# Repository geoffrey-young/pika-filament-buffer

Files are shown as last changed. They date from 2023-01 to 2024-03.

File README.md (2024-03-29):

# piKa - a multimaterial filament buffer solution

---

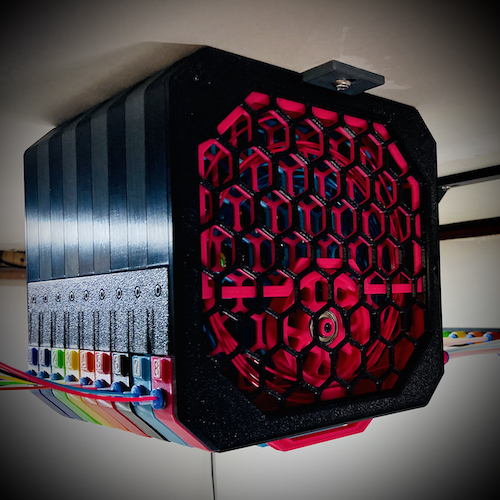
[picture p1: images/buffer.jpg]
buffer
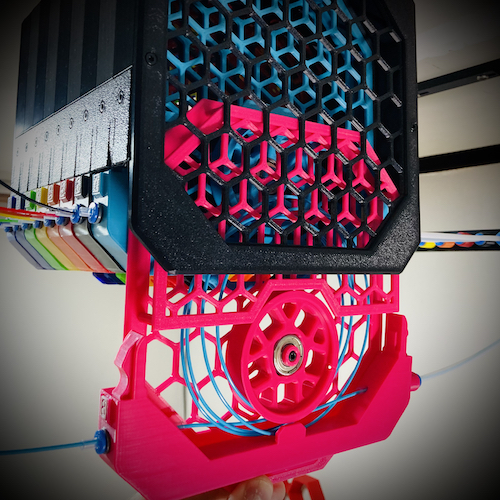
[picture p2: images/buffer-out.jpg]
buffer out
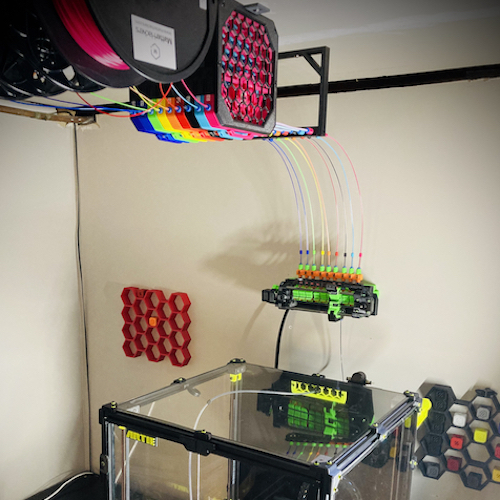
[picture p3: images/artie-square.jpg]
artie
|  |  |  |
| :---: | :---: | :---: |
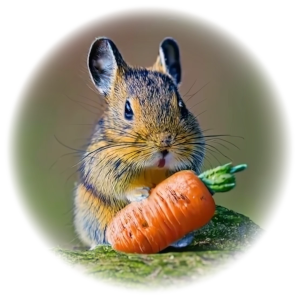
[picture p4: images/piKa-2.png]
piKa
| |  | |

---

## welcome

thanks for checking out [piKa](#pika), the friendly [ercf](https://github.com/EtteGit/EnragedRabbitProject) filament buffer.

now let's get to it...

* [operation](#operation)
* [how much can I buffer?](#how-much-can-i-buffer)
  + [testing](#testing)
  + [limitations](#limitations)
* [BOM](#bom)
  + [a note on magnets...](#a-note-on-magnets)
  + [m2x8 hex cap self threading screws](#m2x8-hex-cap-self-threading-screws)
* [printing](#printing)
* [assembly](#assembly)
  + [manual](#manual)
  + [video](#video)
  + [array](#array)
  + [buffer segments](#buffer-segments)
  + [tag plates](#tag-plates)
* [mounting](#mounting)
* [pictures](#pictures)
* [why?](#why)
* [piKa?](#pika)
* [credits](#credits)
* [contributing](#contributing)
* [other buffer options](#other-buffer-options)

---

## operation

buffer operation made simple...

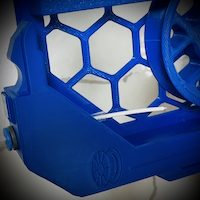
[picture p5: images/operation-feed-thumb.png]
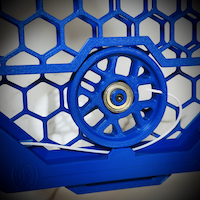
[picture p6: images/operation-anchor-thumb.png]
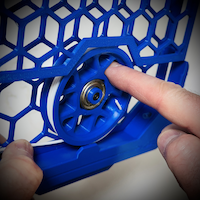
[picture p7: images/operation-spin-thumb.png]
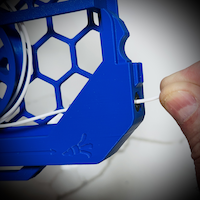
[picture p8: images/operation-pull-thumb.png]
      

there's also a video of the buffer in action I posted on discord that's worth a look:

- https://discord.com/channels/460117602945990666/708772910956937336/1038298353324273754

the number of people who haven't figured out the spin-the-wheel-with-your-finger method is significantly higher than I would have imagined.

"but how fast and easy is it to load... really?" I hear you cry.  allow satisfied discord user `@ningj V2.2726` to show you:

- https://discord.com/channels/460117602945990666/909743915475816458/1089361904650162266

## how much can I buffer?

my `ercf_calib_ref` is currently `1146.4` and I use 5 loops.

beyond that, my tests indicate the [standard wheel](stl/[a]_buffer-wheel_xN.stl) can successfully buffer ~300mm per loop up to 6 loops:

| loops | buffer capacity |
| :---  | :--- |
| 1 | 300mm | 
| 2 | 600mm | 
| 3 | 900mm | 
| 4 | 1200mm | 
| 5 | 1500mm | 
| 6 | 1800mm | 
| 7+ | not recommended | 

### testing

I've added the [klipper macro](./klipper/pika.cfg) I use to test repeated buffer load/unload cycles, which is a great way to exercise your setup without printing.

***!!! you must remove the bowden from the toolhead before running this macro.  you've been warned !!!***

### limitations

pika performance is steady and reliable up to 6 loops, which should provide more than enough for the vast majority of setups.

at 7+ loops two gremlins start to reveal themselves...

the first gremlin is that the filament begins to be more prone to tangling during or after the load sequence.  experimentation has led me to believe this is mostly due to limitations of the [standard wheel](stl/[a]_buffer-wheel_xN.stl) design.

the second gremlin is more insidious in that the weight of the buffered filament begins to compound - once you load 300mm it takes more push to slosh the next 300mm of filament back and coil it up in the cage.  after around 2000mm or so of filament the ercf gear isn't as successful in pushing all the filament along and the consistency of the buffer process begins to degrade.  

the former problem I'm beginning to solve with a [new wheel concept](https://github.com/geoffrey-young/pika-filament-buffer/tree/v2-wheel-beta/v2-wheel-beta), while no wheel design can counteract the laws of physics governing the latter.  I'm still giving this latter gremlin some thought...

## BOM

here is the hardware you'll need.  hopefully this is a full, accurate list...

| item | 3 cart total | 6 cart total | 8 cart total | 9 cart total | 12 cart total |
| :--- | :--- | :--- | :--- | :--- | :--- |
| m3x8 (or m3x10) | 23 | 38 | 48 | 53 | 68 |
| m3x8 (or m3x10) flat head | 6 | 12 | 16 | 18 | 24 |
| m3x12 | 3 | 6 | 8 | 9 | 12 |
| m3 heatset (standard voron m3 x 5mm x 4mm) | 12 | 24 | 32 | 36 | 48 |
| [m2x8 self tapping](#m2x8-hex-cap-self-threading-screws) | 21 | 42 | 56 | 63 | 84 |
| 608 bearing | 3 | 6 | 8 | 9 | 12 |
| ecas connector | 6 | 12 | 16 | 18 | 24 |
| [10x3 disc magnet with 3mm hole](#a-note-on-magnets) (optional) | 6-12 | 12-24 | 16-32 | 18-36 | 24-48 |
| PTFE/FEP 4mm OD x (2.5mm or 3.0mm ID) tubing | variable | variable | variable | variable | variable |

note that all of the m3x8 screw holes are long enough to accept m3x10

plus mounting hardware if you want to use the bottom bracket to mount the array on something.

the majority of the hardware was selected due to it being common across voron builds, so folks will likely have it just sitting around.  the big exception being the hole magnets...

### a note on magnets...

I used 10x3 disc magnets ~~[from amazon]()~~, which seem to be a moving target. basically, you're looking for 10x3 disc magnets with a 3mm hole in the middle, like these:

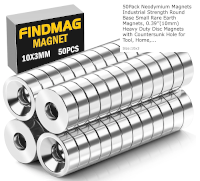
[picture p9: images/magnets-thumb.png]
magnets


magnets with 4mm holes are a little better, but outside of the very first set I ordered I haven't been able to find any.

**just a small wrinkle...** as with the "6x3mm" magnets for the ercf and other voron projects, parts are designed against sizes most commonly provided by suppliers.  in our case, the majority of "10x3mm" hole magnets in the wild are really around 9.5mm in diameter.  as such, piKa parts are designed against this width.

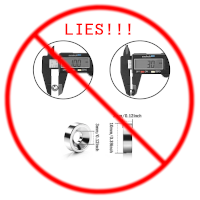
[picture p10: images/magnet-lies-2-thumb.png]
magnet-lies-2
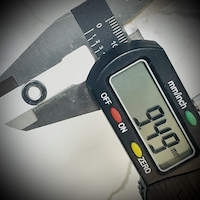
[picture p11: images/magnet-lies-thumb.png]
magnet-lies
 

if you have true 10x3mm magnets they'll be too large for the standard magnet tops and connectors.  the good news is that you now have options.

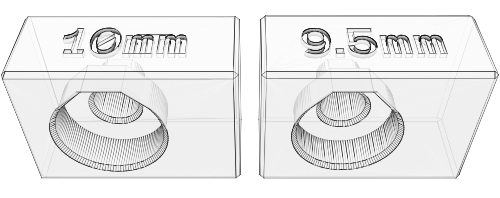
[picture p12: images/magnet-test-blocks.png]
magnet test blocks


after printing the [magnet test blocks](./stl/10mm-magnets/magnet-test-blocks.stl) to verify your fit, the [10mm](./stl/10mm-magnets/) directory has the files you'll need.

### m2x8 hex cap self threading screws

these m2x8 hex cap self threading screws [from amazon](https://www.amazon.com/gp/product/B00YBMRAH4) are really handy, both for this and other voron projects, like klicky.  m2x10 will also work if those are easier to find.  

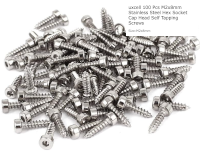
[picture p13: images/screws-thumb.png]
screws


## printing

a few things to note when printing...

- **the models already oriented for optimal printing**.  no parts have included supports to remove, nor are supports necessary for any part.  if there are overhangs that need support the part is oriented incorrectly.
- due to bending of large parts, you want to **print the bottoms flat so that the latch fit is tight** - you'll only be able to print 1 or two of these at a time.
- conversely, **the tops are designed to be printed upright**, so go ahead and fill your plate.  if you care about a good looking bottom overhang, keep your exterior perimeter fans at 100% and engage them starting on layer 2.
- I used 20% infill on the tops and bottoms in order to keep parts light and plastic use down.  **ymmv**.
- I would suggest printing the latches and bracket using standard voron parameters (40% infill, .2mm layers, 4 perimeters) for added strength.
- the screen with the posts works best with higher temps and lower fan to keep the layers as strong as possible.  early versions had thinner posts, but the current version is a bit more rigid and should be less problematic.
- consider using setting `only_one_perimeter_first_layer` to `true` for the screens, which helps the first layer be a little more sane.  well, in superslicer, anyway.

I printed mine in ABS, and most people do the same.  PLA should be fine, but ymmv...

## assembly

hopefully, y'all find this self explanatory, and can figure it out from the pictures.  basically, we have:

- a series of buffer slot slider thingies
- held together by a frame

that's about it.

the good news is that there's only one way the parts can really go together, and everyone so far has found it relatively straightforward.

and in late breaking news, there's even [a manual](./assembly-manual.pdf) and a [video][#video]!

feel free to ping me on the [voron discord](https://discord.com/channels/460117602945990666/869236671554682990) in [`#ercf_questions`](https://discord.com/channels/460117602945990666/909743915475816458) if you have issues.  

### manual

and now... [a manual](./assembly-manual.pdf)

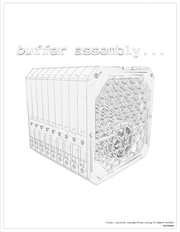
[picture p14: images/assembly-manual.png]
manual


### video

recently, @MakerMylo created a [video](https://youtu.be/PdVolU5ywEg) of an [8 cart pika build](https://www.printables.com/model/776988-8-lane-pika-filament-buffer-ercf-v2) which you may find helpful as well.

### array

currently, there are 6, 9, and 12 slot versions for [ERCF classic](https://github.com/EtteGit/EnragedRabbitProject), plus an 8 cart version for [ERCF v2](https://github.com/Enraged-Rabbit-Community/ERCF_v2).

the only parts that differ depending on the number of slots are the side latches and bottom bracket.

the 9 cart is the most popular, and what I currently run. both the 6 and 12 cart versions have at least one user I've worked through the design with, so I'm confident in the dimensional accuracy. however, if you discover an issue with the sizing just let me know.

| part | description | required hardware | 
| :--- | :--- | :--- |
| [`array-front.stl`](stl/array-front.stl) | front of array | m3x8 (or m3x10) | 
| [`array-front-screen.stl`](stl/array-front-screen.stl) | screen for front of array | none | 
| [`array-back.stl`](stl/array-back.stl) | back of the array | m3x8 (or m3x10) |
| [`array-latch-9a.stl`](stl/array-latch-9a.stl) | side latch (stls for 3, 6, 8, and 12 cart versions also provided) | m3x8 (or m3x10) |
| [`array-latch-9b.stl`](stl/array-latch-9b.stl) | side latch (stls for 3, 6, 8, and 12 cart versions also provided) | m3x8 (or m3x10) |
| [`array-bottom-bracket-9.stl`](stl/array-bottom-bracket-9.stl) | bottom bracket (stls for 3, 6, 8, and 12 cart versions also provided) | m3x8 (or m3x10) |

### buffer segments

one complete buffer is required per cart, so for a nine cart system `_xN` turns in to `_x9` and you print 9 of that piece.

two buffer top configurations are provided:

* [one ecas end and one disc magnet end](stl/[a]_buffer-top-ecas+magnet_xN.stl)
* [two disc magnet ends](stl/[a]_buffer-top-magnet+magnet_xN.stl)

which configuration you choose depends on the needs of your setup.  

please see [the note on magnets](#a-note-on-magnets), and check out the [10mm magnet options](./stl/10mm-magnets/) as required. 

| part | description | required hardware |
| :--- | :--- | :--- |
| [`buffer-bottom_xN.stl`](stl/buffer-bottom_xN.stl) | segment bottom | m3 heatset |
| [`[a]_buffer-top-ecas+magnet_xN.stl`](stl/[a]_buffer-top-ecas+magnet_xN.stl) | segment top, one side ecas and one side disc magnet connector | ecas, [9.5mm disc magnet](#a-note-on-magnets) |
| [`[a]_buffer-top-magnet+magnet_xN.stl`](stl/[a]_buffer-top-magnet+magnet_xN.stl) | segment top, both sides disc magnet connector | ecas, [9.5mm disc magnet](#a-note-on-magnets) |
| [`[a]_ecas-to-magnet-end_xN.stl`](stl/[a]_ecas-to-magnet-end_xN.stl) | if you use either of the magnet tops | ecas, [9.5mm disc magnet](#a-note-on-magnets) |
| [`[a]_buffer-screen-a_xN.stl`](stl/[a]_buffer-screen-a_xN.stl) | segment screen for wheel | m3x8 (or m3x10) flat head, m3 heatset |
| [`[a]_buffer-screen-b_xN.stl`](stl/[a]_buffer-screen-b_xN.stl) | segment top screen | [m2x8 self tapping](#m2x8-hex-cap-self-threading-screws) |
| [`[a]_buffer-bearing-insert_xN.stl`](stl/[a]_buffer-bearing-insert_xN.stl) | holds the wheel in place | m3x12 |
| [`[a]_buffer-handle_xN.stl`](stl/[a]_buffer-handle_xN.stl) | segment handle | m3x8 (or m3x10) |
| [`[a]_buffer-wheel_xN.stl`](stl/[a]_buffer-wheel_xN.stl) | wheel | 608 bearing |

the wheel is (currently) almost exactly the same as the ercp wheel...  however, I strongly suggest *not* using the stock ercf wheel - the pika wheel has a slightly different bearing offset so that it sits next to the screen properly, as well as a hole for loading so you are less likely to cross filament on the wheel.

### tag plates

if you mount your buffer overhead your numbers will be upside down.  you can find upside down tag plates [here](https://github.com/geoffrey-young/3D-Printing/tree/main/models/voron/ercf/upside-down-numbers).

## mounting

in general I'm not a fan of sticking the ercf on my printer - something just makes me think all that extra weight and loose pieces rattling around can't be good for my resonance compensation efforts.

with that in mind, I mount my ercf on the wall at 90 degrees using a french cleat system, which you can find [here](https://github.com/geoffrey-young/3D-Printing/tree/main/models/voron/ercf/mounts/ercf-french-cleat).

the 90 degree mounting created some challenges accessing the filament block ecas connectors, so I made [an extension](https://github.com/geoffrey-young/3D-Printing/tree/main/models/voron/ercf/extender) to help.

a magnetic bowden "bridge" (plus some springs) keeps my bowden tubes straight, clear, and managed.  available [here](https://github.com/geoffrey-young/3D-Printing/tree/main/models/voron/ercf/mounts/bridge).

## pictures

some reference photos, videos, etc

| artie `v2.1650` | | |
| :--- | :--- | :--- |
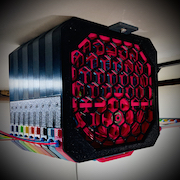
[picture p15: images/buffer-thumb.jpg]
buffer
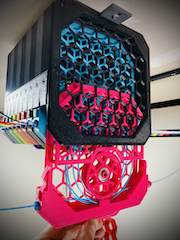
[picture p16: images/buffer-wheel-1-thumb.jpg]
buffer wheel
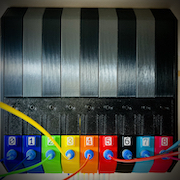
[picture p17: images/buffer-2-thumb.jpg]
buffer 2
|  |  |  |
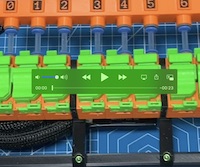
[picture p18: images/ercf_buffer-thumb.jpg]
movie (https://discord.com/channels/460117602945990666/708772910956937336/1038298353324273754)
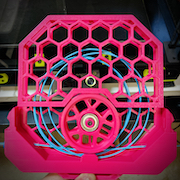
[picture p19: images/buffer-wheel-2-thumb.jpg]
buffer wheel 2
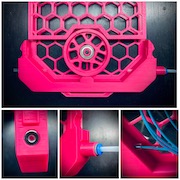
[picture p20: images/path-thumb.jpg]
path
|  |  |  |
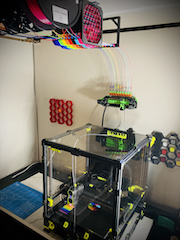
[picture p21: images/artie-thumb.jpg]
artie
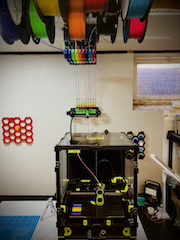
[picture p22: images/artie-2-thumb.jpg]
artie 2
|  |  | assembly manual |

| other users on discord | | |
| :--- | :--- | :--- |
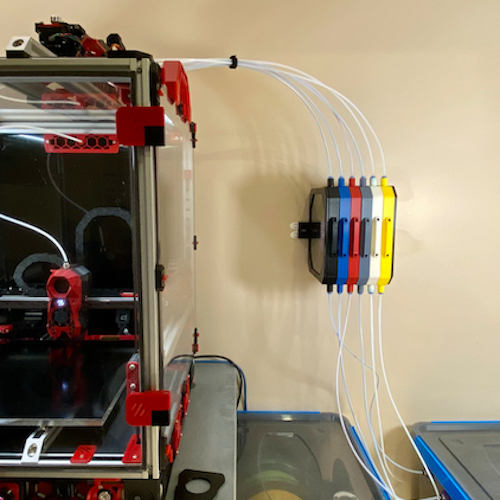
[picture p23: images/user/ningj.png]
ningj-1
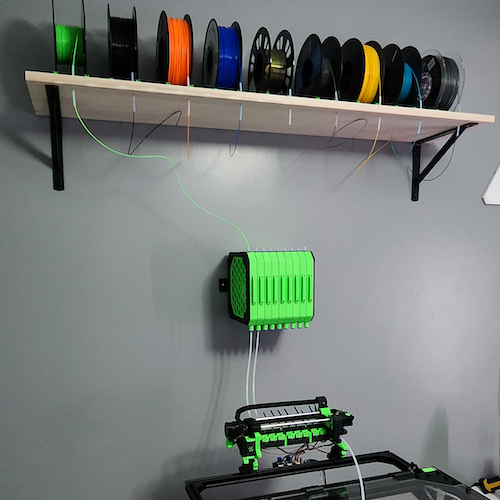
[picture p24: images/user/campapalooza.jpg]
campapalooza-1
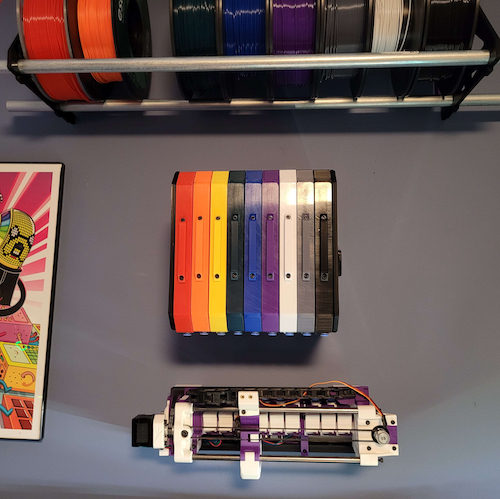
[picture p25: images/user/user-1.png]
user-1
|  |  |  |
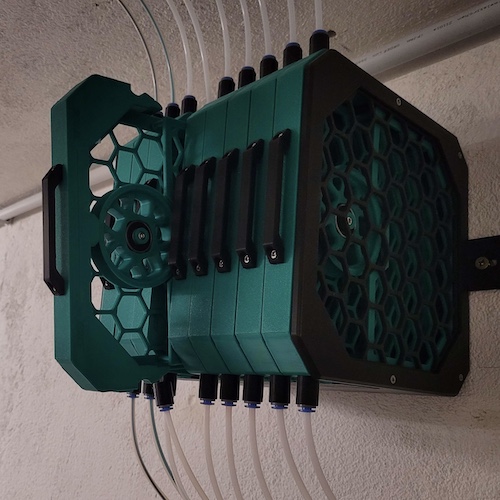
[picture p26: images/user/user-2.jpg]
user-2
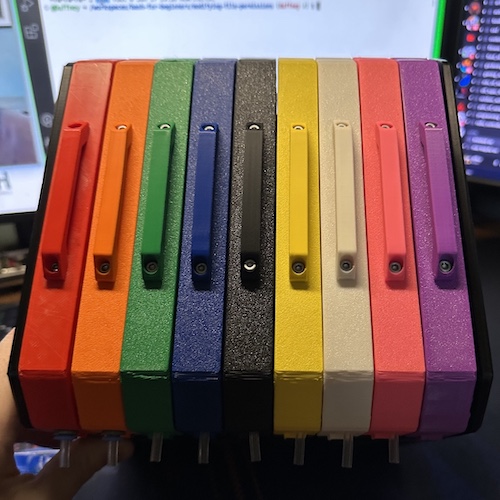
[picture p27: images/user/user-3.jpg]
user-3
|  |  | |

pull requests against the [current development branch](#contributing) with your (single 500x500px) picture added to `images/user/` most welcome.

## why?

filament buffers are hard™

I didn't realize how hard until I ventured down this path.

I started like most do, and loyally printed some [ercf carrot patch](https://github.com/EtteGit/EnragedRabbitProject/tree/main/Carrot_Patch) units.  space limitations required me to mount them overhead, which is where things started to go sideways - every time I needed to put in new filament I had to find a chair and fsck around with the confined carrot patch space, sharp edges, filament whiplash, and whatnot - all overhead - until my shoulders hurt, cursing the entire time.  I figured there had to be a better way...  

it turns out, there really wasn't...  at least not at the time.  since then, the community has been kind enough to generate a few [different buffer options](#other-buffer-options), each with its unique set of benefits and drawbacks depending on your needs, setup, and tolerance.  all of them are better than the original ercp, imho, which is good for everyone.  however, I'm of the opinion that they all still have drawbacks, leaving us still chasing the platonic ideal filament buffer solution...

still, way back then all I wanted was a lightning-fast, super-simple, overhead-mounted, expletive-free, wheel-based, wicked-dependable filament buffer solution.  how hard could it be?

this thing here is where I ended up.

honestly, I'm surprised it actually worked... but it really does, and my experience has been frustration free ever since.  others on discord seem to have similarly joyful experiences with it as well, so I guess I'm on to something.

## piKa?

### ***in chemistry...***

a [buffer](https://en.wikipedia.org/wiki/Buffer_solution) is a solution specifically designed to be resistant to changes in pH, allowing a reaction to continue in balance even when ideal conditions are threatened.  the most effective buffers  - those with the greatest capacity to absorb change - are created using an acid whose **p**___Ka___ (acid dissociation constant) is equal to the desired pH.  choosing an acid with the wrong **p**___Ka___ can mean disaster.

**p**___Ka___ is crucial to buffer efficacy

### ***in taxonomy...***

three members make up the order [Lagomorpha](https://en.wikipedia.org/wiki/Lagomorpha): rabbits, hares… and pikas

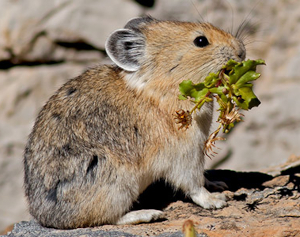
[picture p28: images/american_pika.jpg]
american pika (https://www.nwf.org/Educational-Resources/Wildlife-Guide/Mammals/American-Pika)

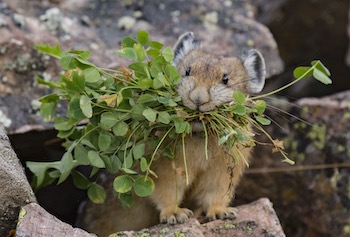
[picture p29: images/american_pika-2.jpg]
american pika (https://www.biographic.com/dine-and-dash/)


pretty cool little creatures, worth getting to know.

### ***in multimaterial 3d printing...***

we have a [rabbit](https://github.com/EtteGit/EnragedRabbitProject), and a [hare](https://github.com/moggieuk/Happy-Hare), and now... a pika

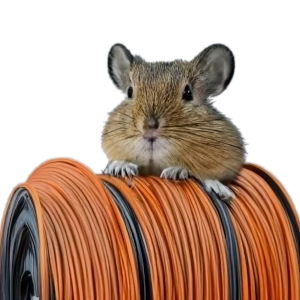
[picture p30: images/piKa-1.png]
piKa


buffers, solutions, p*Ka*... the name just seemed to come together for a recovering chemist.

## credits

- the entire concept here started after seeing [this mmu buffer on printables.com](https://www.printables.com/model/30811-mmu-slot-buffer).  while my work isn't really a mod of that (I modeled everything myself from scratch), I did copy the latch concept nearly... verbatim?  I'm sure there's a word for it.  anyway, the latch works really well, and needless to say I couldn't have figured a mechanism like that on my own.  this project owes sincere credit and gratitude to all the work and effort over there.  many thanks!

- all the fittings and cutouts - ecas and m3 holes, bridging, etc - were taken directly from either the [ercf project](https://github.com/EtteGit/EnragedRabbitProject) or the [voron 2.4 project](https://github.com/VoronDesign/Voron-2/).  since I use blender and don't cad, I really appreciate all the community work that has gone into getting those measurements and fit tricks just right.  kudos to team voron, be they enraged or not.

- the buffer wheel is taken right from [ercf project](https://github.com/EtteGit/EnragedRabbitProject).  no need to reinvent the wheel...

- [deepfriedhero](https://dfh.fm), [west3d](https://west3d.com), and [fabreeko](https://www.fabreeko.com) for consistently fantastic parts and service

- I'm super grateful for some early beta testers, who provided really valuable feedback:
  - `@TheTechRunner V2.1453 V0.1556`
  - `@ningj V2.2726`
  - `@ZChem V2.5299`
  - `@SilentMuse V2.3841`
  - `@Imburr VT.959`
  - `@xF4m3 V2.3687`

- probably others - if you feel left out let me know :)

## contributing

pull requests against [the `dev` branch](https://github.com/geoffrey-young/pika-filament-buffer/tree/v2-wheel-beta/) more than welcome.  feel free to dm me over in discord to discuss something first.

be sure to read the [LICENSE](./LICENSE) and mentally agree with it.  please don't make me add license acknowledgement and sign-off overhead to the project - we're all just after a kinder buffer experience so we can get on with printing, so let's just focus on that, ok?

## other buffer options

some other community buffers that may suit your needs:

- [carrot quiver](https://github.com/SkiBikePrint/ERCF_Mods/tree/main/Carrot_Quiver_Buffer)
- [stern wheeler](https://www.printables.com/model/472316-stern-wheeler)
- [cotton tail](https://github.com/Enraged-Rabbit-Community/ERCF_v2/blob/master/Recommended_Options/ERCT_Buffer)

I suggest asking on discord about these other buffers and their strengths and weaknesses and decide what buffer is best for your situation.

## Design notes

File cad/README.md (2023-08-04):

# where's the CAD?

I do all my modeling with [blender](https://www.blender.org), so there are unfortunately no CAD files for sharing.

someday I may learn CAD... but probably not

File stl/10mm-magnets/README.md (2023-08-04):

# 10x3mm magnet support

as discussed in [a note on magnets...](../../README.md#a-note-on-magnets) in the [README](../../README.md), true 10x3mm disc magnets are a rare find in the wild.  however, if you happen to get some below are the files you'll need.

please print the [disc magnet test blocks](./magnet-test-blocks.stl) and test fit your magnets before printing actual parts.

magnet test blocks

---

| part | description |
| :--- | :--- |
| [`[a]_10mm-buffer-top-ecas+magnet_xN.stl`](stl/10mm-magnets/[a]_10mm-buffer-top-ecas+magnet_xN.stl) | segment top, one side ecas and one side 10x3mm disc magnet connector |
| [`[a]_10mm-buffer-top-magnet+magnet_xN.stl`](stl/10mm-magnets/[a]_10mm-buffer-top-magnet+magnet_xN.stl) | segment top, both sides 10x3mm disc magnet connector |
| [`[a]_10mm-ecas-to-magnet-end_xN.stl`](stl/10mm-magnets/[a]_10mm-ecas-to-magnet-end_xN.stl) | if you use either of the magnet tops |

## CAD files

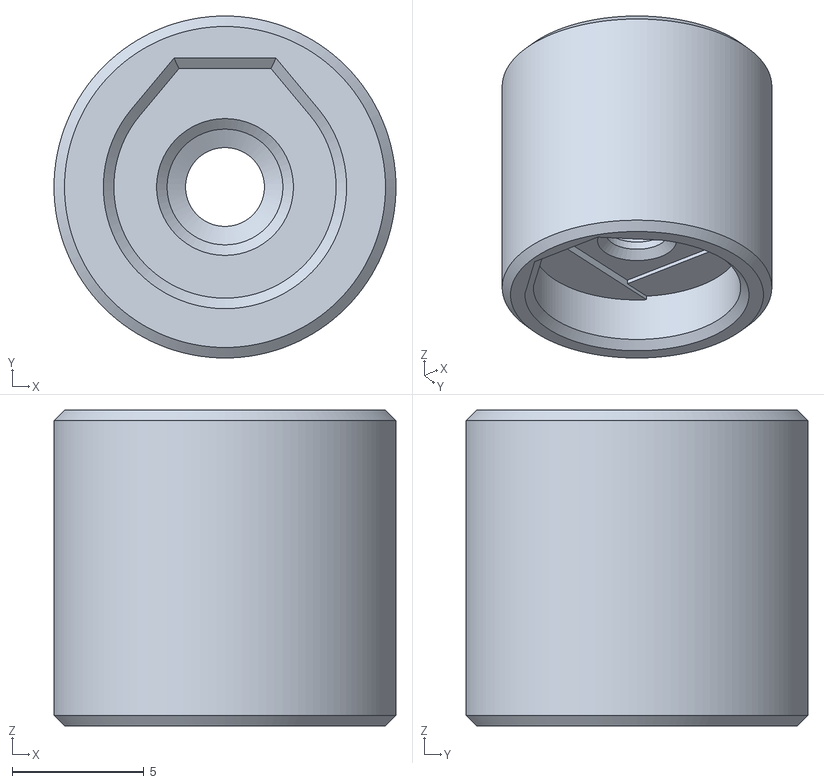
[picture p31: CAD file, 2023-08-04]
stl/10mm-magnets/[a]_10mm-ecas-to-magnet-end_xN.stl
13.0 x 13.0 x 12.0

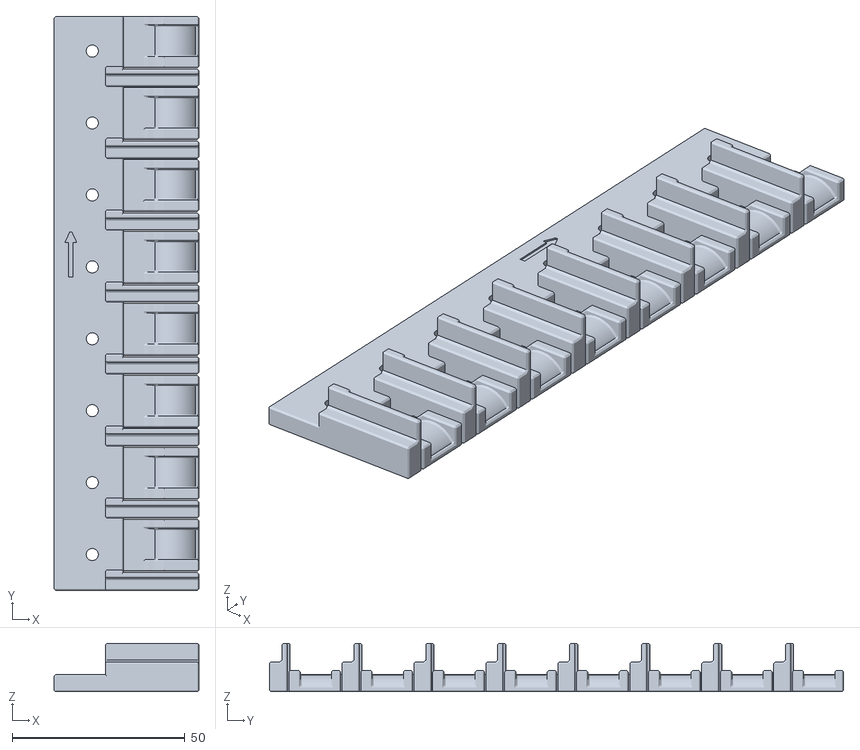
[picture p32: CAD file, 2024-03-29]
stl/array-latch-8a.stl
41.8 x 166.0 x 14.0

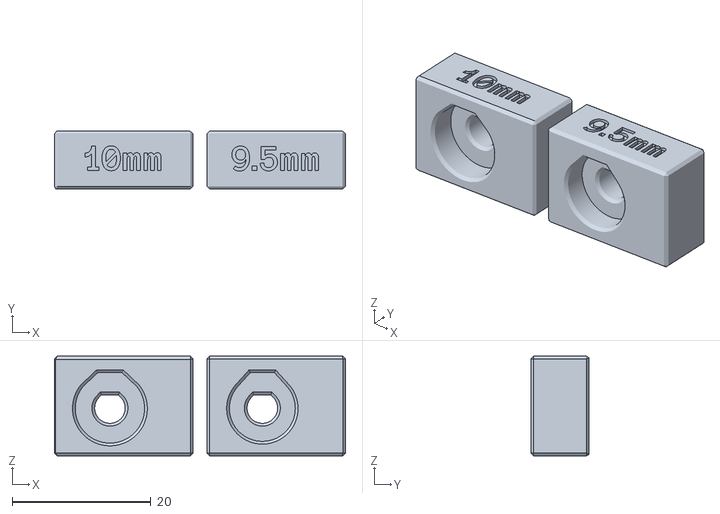
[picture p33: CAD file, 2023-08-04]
stl/10mm-magnets/magnet-test-blocks.stl
42.0 x 8.40 x 14.4

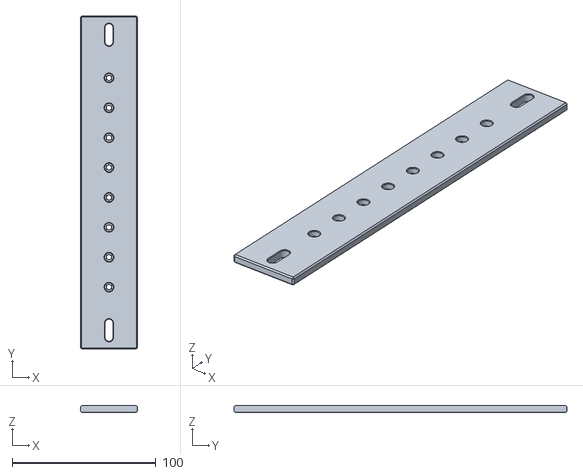
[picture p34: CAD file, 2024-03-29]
stl/array-bottom-bracket-8.stl
39.8 x 231.7 x 4.80

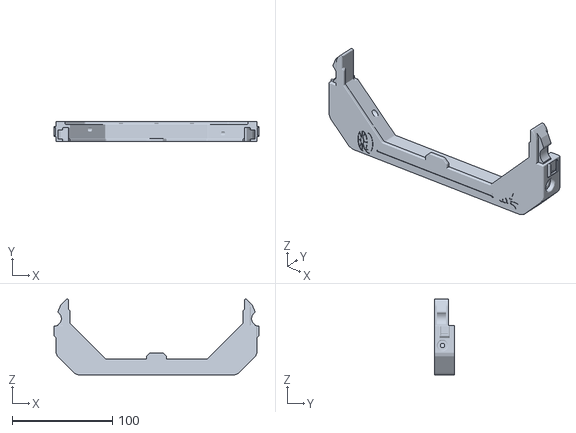
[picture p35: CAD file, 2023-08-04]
stl/10mm-magnets/[a]_10mm-buffer-top-magnet+magnet_xN.stl
204.0 x 20.0 x 75.4

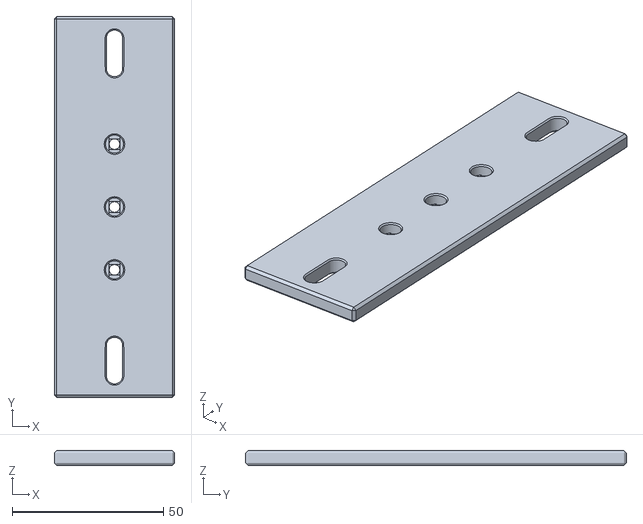
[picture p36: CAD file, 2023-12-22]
stl/array-bottom-bracket-3.stl
39.8 x 126.0 x 4.80

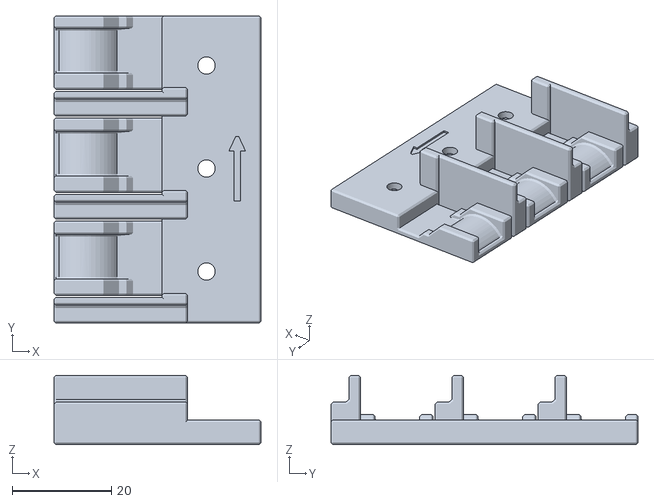
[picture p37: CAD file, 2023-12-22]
stl/array-latch-3b.stl
41.8 x 62.0 x 14.0

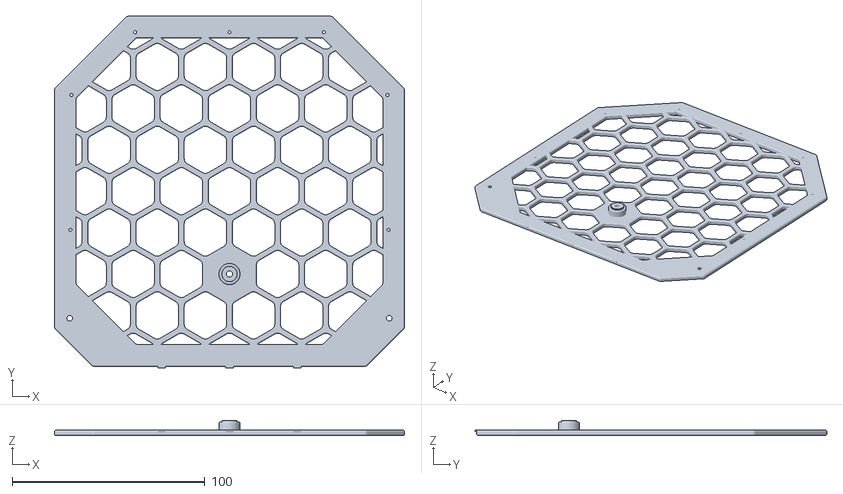
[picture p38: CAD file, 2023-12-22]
stl/[a]_buffer-screen-a_xN.stl
182.0 x 182.8 x 7.80

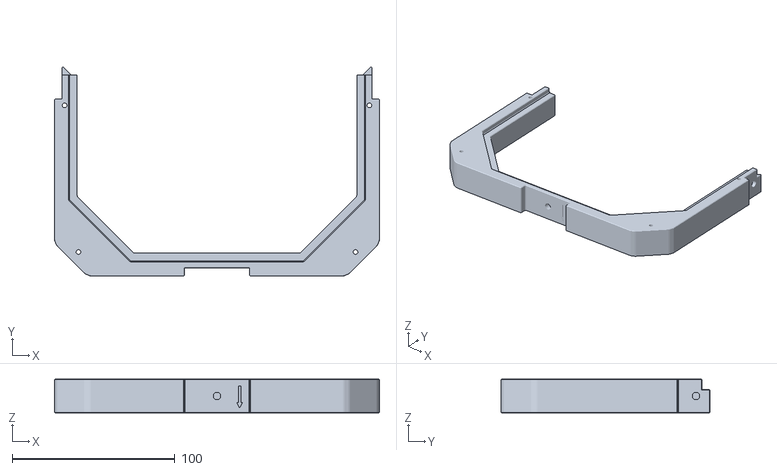
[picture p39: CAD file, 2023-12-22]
stl/buffer-bottom_xN.stl
200.0 x 128.6 x 20.8

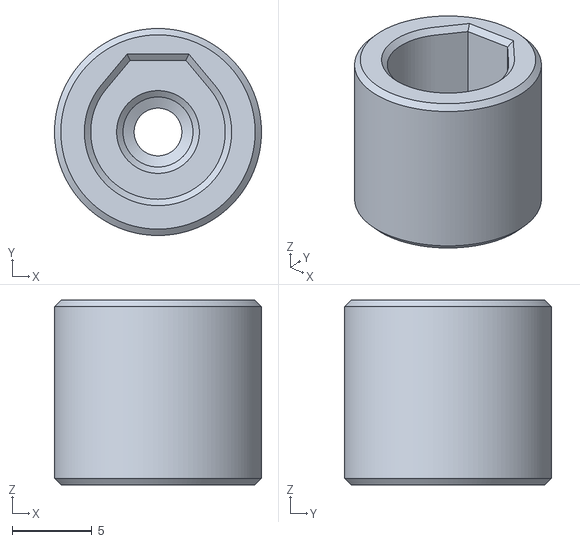
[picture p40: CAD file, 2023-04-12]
stl/[a]_ecas-to-magnet-end_xN.stl
13.0 x 13.0 x 11.6

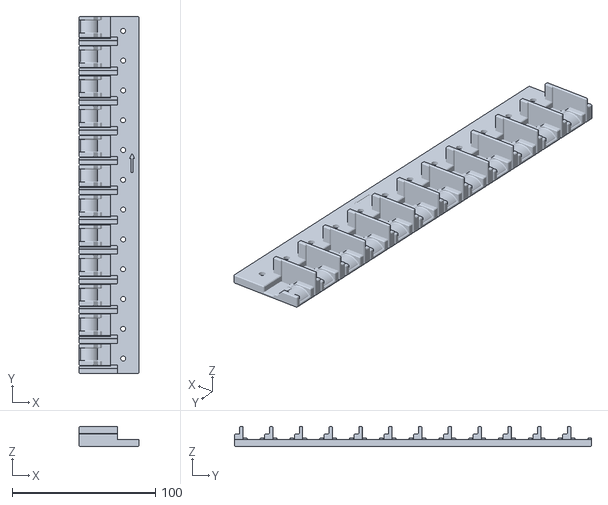
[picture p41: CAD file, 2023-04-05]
stl/array-latch-12b.stl
41.8 x 249.2 x 14.0

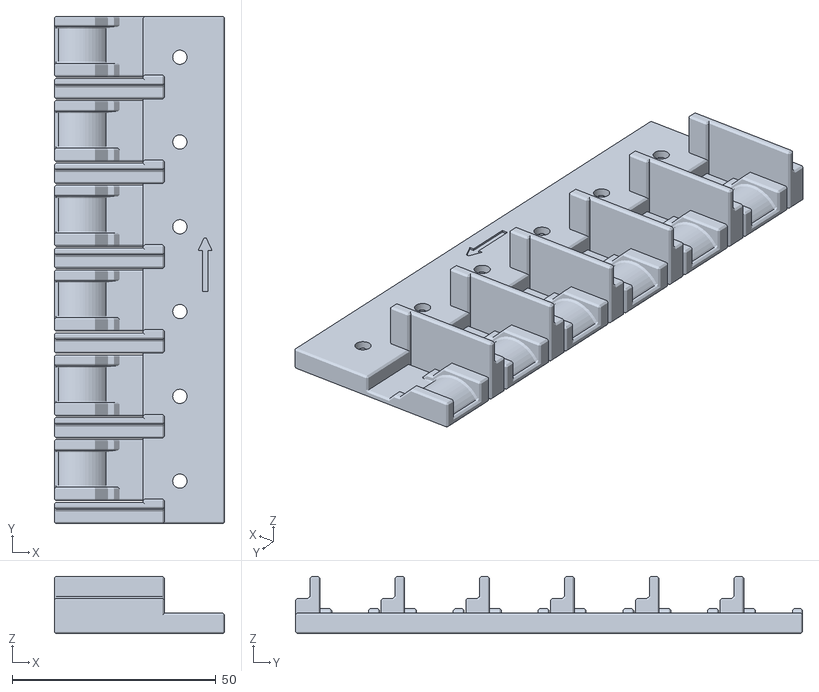
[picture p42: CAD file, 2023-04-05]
stl/array-latch-6b.stl
41.8 x 124.4 x 14.0

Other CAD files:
stl/array-latch-8b.stl
stl/10mm-magnets/[a]_10mm-buffer-top-ecas+magnet_xN.stl
stl/array-latch-3a.stl
stl/[a]_buffer-top-ecas+magnet_xN.stl
stl/[a]_buffer-top-magnet+magnet_xN.stl
stl/array-latch-6a.stl
stl/[a]_buffer-bearing-insert_xN.stl
stl/[a]_buffer-handle_xN.stl
stl/[a]_buffer-screen-b_xN.stl
stl/[a]_buffer-wheel_xN.stl
stl/array-back.stl
stl/array-bottom-bracket-12.stl
stl/array-bottom-bracket-6.stl
stl/array-bottom-bracket-9.stl
stl/array-front-screen.stl
stl/array-front.stl
stl/array-latch-12a.stl
stl/array-latch-9a.stl
stl/array-latch-9b.stl

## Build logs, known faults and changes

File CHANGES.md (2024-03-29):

# changes, etc
---

## r4 (tbd)
- reduced heatset holes to 4.6mm diameter
- add 3 cart latches and bottom (https://github.com/geoffrey-young/pika-filament-buffer/pull/9)
- add 8 cart latches and bottom for ERCF v2

## r3 (20230804)
##### release: [r3](https://github.com/geoffrey-young/pika-filament-buffer/releases/tag/r3)

- added support for true 10x3mm magnets *(thanks @Gandalf and @xF4m3)*
- extended m3x8 holes to m3x10 *(thanks @mortis_robotum and @pinched_nerve)*
- removed ecas+ecas option (you'll all thank me later)

## r2 (20230529)
##### release: [r2](https://github.com/geoffrey-young/pika-filament-buffer/releases/tag/r2)

- welcome pika! ([discord announcement](https://discord.com/channels/460117602945990666/909743915475816458/1102319721040334949))
- [replace screen m3 nuts with heatsets](https://github.com/geoffrey-young/pika-filament-buffer/pull/3) *(thanks [BRueter](https://github.com/brueter/))*

---
## initial release (20230407)
##### release: [r1](https://github.com/geoffrey-young/pika-filament-buffer/releases/tag/r1)

first official github release!

special thanks to everyone who helped troubleshoot, support, and improve this little project.  I don't know what we'll do with all our free time, now that we're not wrestling with buffers every 5 minutes...

in no particular order:
- @TheTechRunner V2.1453 V0.1556
- @ningj V2.2726
- @ZChem V2.5299
- @SilentMuse V2.3841
- @xF4m3 V2.3687
- @anxman
- @Imburr VT.959
- @xF4m3 V2.3687

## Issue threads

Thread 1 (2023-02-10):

buffer-bearing-insert.stl - end snaps off

whi-tw, 2023-02-10:
Hello! This looks amazing - printing the parts now!

I've had the exact same problems as you described - accessing the wheel on the other buffer solutions leads to so much frustration and shouting, my wife wants to yeet the whole thing out the window.

I've got the first buffer set up, but keep having the end of the `buffer-bearing-insert.stl` snapping off, which means the wheel comes off the axle, leading to all sorts of misery. Is this a common problem / is there a solution? I'm thinking of maybe trying replacing the axle with an M5 screw (with a printed spacer, so the wheel fits snugly around it and a washer to avoid this, but wondered if this is something that you / testers ever came across, and if I'm doing something wrong!

whi-tw, 2023-02-10:
I think I know the problem - mocking something up and will get back to you

whi-tw, 2023-02-10:
I think I've got a solution.

The existing part looks like this when put together - note the space between `buffer-screen-a` and `buffer-bearing-insert` inside the bearing:
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

My solution is to make `buffer-bearing-insert` longer, meaning that it butts up against `buffer-screen-a`, so the two parts clamp down against each other when the M3 screw is tightened:
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

I've modeled this, and the `.stl` and `.step` are available here: [longer-buffer-bearing-insert.zip](https://github.com/geoffrey-young/filament-buffer/files/10707773/longer-buffer-bearing-insert.zip) ([onshape project](https://cad.onshape.com/documents/82f0ecece68e89c47fa1ffab/w/8ff1339605c828d3a5af0040/e/4c220e18b0531cc9d481d5e8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)).

geoffrey-young, 2023-02-22:
hi :)

it’s pretty simple to make the bearing insert longer.  in my own setup there is no space, so maybe you have different sized bearings?  can you provide some measurements of the bearings, and maybe some images of the bearing in the wheel?

whi-tw, 2023-02-24:
It’s a 608ZZ bearing - I’ll send a picture when I’m next by the printer!It looks exactly like the cross section in the image though. I bought the bearings for the ERCF buffers, and thought they’d be the same ones for this - I believe you said it’s the same wheel, just with a hole bored through for loading (amazing idea btw - works super well!)On 22 Feb 2023, at 04:00, Geoffrey Young ***@***.***> wrote:
hi :)
it’s pretty simple to make the bearing insert longer.  in my own setup there is no space, so maybe you have different sized bearings?  can you provide some measurements of the bearings, and maybe some images of the bearing in the wheel?

—Reply to this email directly, view it on GitHub, or unsubscribe.You are receiving this because you authored the thread.Message ID: ***@***.***>

geoffrey-young, 2023-02-25:
ok, try the `m5-bearing` branch and [buffer-screen-b-m5.stl](https://github.com/geoffrey-young/filament-buffer/blob/m5-bearing/stl/buffer-screen-b-m5.stl).  I'm not sure how standard m5x12 button head screws are, but if you have any sitting around this setup should be a bit stronger.  let me know how it works out :)

whi-tw, 2023-03-07:
Sorry it's taken so long to get back to you.

what kind of bearing are you using? I'd assume they are flush with the flat parts of the filament walls like mine are?

I can't see how there could possibly be no space between the bearings, unless your bearings are ~5mm thick? AFAIK 608 bearings are 7mm thick as standard, so surely there must be a gap?

geoffrey-young, 2023-03-21:
fixed

Closed 2023-03-21.

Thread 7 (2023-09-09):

Comments on beta wheel

TypQxQ, 2023-09-09:
I love the new beta wheel. From what I've tested so far it works much better than the original. I found the direction of filament important, going from outside to inside (the lip). I also made a smal guide on mine and a visualization window.
I had made my buffer much larger but now with the new wheel I think I can go back to original size. I'm attaching some photos.
Great work!
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

geoffrey-young, 2023-09-10:
glad to hear it's working out.

are you at a booth somewhere?

TypQxQ, 2023-09-10:
> are you at a booth somewhere?

No. If you refer to the stickers on the printer, it's from old shows I've displayed it on. But the printer is so big I have to remove the door frame to get it out of the room 😄

TypQxQ, 2023-09-14:
Just an update, it didn't work as well as I hoped. It's better but the filament still tangles. I have reverese engineered the wheel and I'm trying some alternatives. Here's the original wheel in CAD if intrested:
https://github.com/TypQxQ/pika-filament-buffer/tree/main/cad

smumriak, 2023-10-19:
Unfortunately, neither original wheel nor the beta wheel allow me to use the pika buffer with more than 4 loops. Specifically with ABS filament. Tangles usually 30-40 minutes into print

geoffrey-young, 2023-11-04:
I'm going to close this out, in favor of continuing discussion on Discord.

Closed 2023-11-04.

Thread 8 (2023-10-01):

3 slot version?

Krakert, 2023-10-01:
I would like to see a 3 slot version please, I want to mount 3 spools at each side of my printer, with a buffer. So A 3 slot version would be really helpful!

ronpandolfi, 2023-10-10:
I am actively building a 2x3 myself now. I remodeled some parts here: https://www.printables.com/model/610307-pika-filament-buffer-3x-parts

Krakert, 2023-10-15:
@ronpandolfi great work, maybe a idea to open a pull requests to add the files to the repo?

ronpandolfi, 2023-10-15:
> @ronpandolfi great work, maybe a idea to open a pull requests to add the files to the repo?

Will do.

I'm also currently testing a special mounting bracket for putting a 3x module on each side of an ERCF. It fits well on a V2 300, with space for a spool rack at the rear. I think this fits more as a "mod" though, since the layout is fairly specific.

geoffrey-young, 2023-11-04:
I added 3 cart files to the dev branch. Please let me know if they work ok, then I'll merge to main.

geoffrey-young, 2023-12-17:
closing

Closed 2023-12-17.

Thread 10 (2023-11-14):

Recessed magnet buffer tops

IRTrail, 2023-11-14:
I added a 5mm deep counterbore around the magnet attach points in the buffer tops. This stabilizes the bowden tube in situations where it isn't a straight out attachment. My tubes curve just enough the magnets don't hold them square, this solves that situation. I only did the 10mm magnet-magnet version, but if you want me to CAD up the others, let me know. Probably inbox at discord (silverback_attack) is best because I am not great with github yet.

See attachment.
[[a] 10mm Buffer Top Magnets Recessed.zip](https://github.com/geoffrey-young/pika-filament-buffer/files/13343832/a.10mm.Buffer.Top.Magnets.Recessed.zip)

geoffrey-young, 2023-12-17:
I'm not sure I fully understand, but I'll take a look at the stls after the new year

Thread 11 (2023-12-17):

Curiosity : What other mods do you have on your Bowden Tubes?

LostFool, 2023-12-17:
I see some unique items for your bowden connections to the ERCF. Can you share?
Also love this buffer system. i think you should incorporate issue #10, the recessed magnet buffer tops.
I'm also considering spinning up the CAD for you. I am a mechanical designer and would love to give back somehow. I just can't promise time frames, busy daddy life, shop life, 40hours too much work life.

Referencing this picture : https://github.com/geoffrey-young/pika-filament-buffer/blob/main/images/artie-square.jpg

geoffrey-young, 2023-12-17:
everything I use on my ercf can be found here: https://github.com/geoffrey-young/3D-Printing/tree/main/models/voron/ercf

thanks for the offer of cad help.  it's probably a wasted effort, as I'd need to verify each part in blender since that's my workflow engine, and any changes I wouldn't really be able to port back.

happy to chat over on discord :)

LostFool, 2024-01-06:
Thank you, appreciate the reply. sorry for my slow response, hardly enough time for anything in the day.

Closed 2023-12-17.

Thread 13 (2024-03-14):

filament getting under buffer wheel

cdedwards, 2024-03-14:
Any chance of adding a small circle around the buffer wheel with about 1.5 to 2mm height? This would prevent filament from getting under the wheel causing havoc.

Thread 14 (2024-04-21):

Compatibility with endless spool

igiannakas, 2024-04-21:
When endless spool triggers, the leftover filament is pushed back into the pika buffer. However as it isn’t coiled any more it lumps together in a random manner, with the edge of the filament sometimes poking through a neighbouring spool.

This can cause a tangle when the next roll is unloaded and reloaded.

I think a solution to this would be to make the back walls a couple of layers solid. This would stop the filament from intruding the next, neighbouring buffer.

thoughts?

igiannakas, 2024-04-22:
Something like this would help a lot containing the filament within its own cart and stopping it going to the next cart when pushed back to the cartridge when endless spool triggers :)
[Pika screen solid.stl.zip](https://github.com/geoffrey-young/pika-filament-buffer/files/15059280/Pika.screen.solid.stl.zip)

Solid wall is 3 layers deep, so not a huge amount of extra material but enough to prevent the filament from going to the wrong places :)

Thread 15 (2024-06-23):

Other Mounting Options?

MuddyPuddles4325, 2024-06-23:
One thing that would be nice are alternate mounting options, perhaps moving the mounting plate from the bottom to one of the other sides.

I currently have my mounting plate attached through the same screws as the clip plate to mount it directly under a shelf, it works great with the exception it is no longer flush and causes a bit of wiggle.

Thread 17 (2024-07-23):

Screen 'a' has a generic M2 bolt that you can use

NNGB-kor, 2024-07-23:
Instead of self-tapping M2 bolts, we modified the model a bit to use regular M2 bolts, which many people likely own.

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

There is room for a typical hex M2 bolt head, and the and a 2.2 mm hole is drilled.

[[a]_buffer-screen-a_M2.zip](https://github.com/user-attachments/files/16345571/a._buffer-screen-a_M2.zip)

Maybe it will help someone.

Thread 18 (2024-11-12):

New Wheel V2 / Buffer Top missing magnet+magnet option

fmaranhao, 2024-11-12:
Hi,

I decided to try the V2 wheel and the other improvement parts. I downloaded the Buffer Top magnet+magnet and printed 8 at once. When it was finished I noticed they are ECAS+magnet!

I thought I mistakenly added the wrong file to the slicer, but then I noticed the magnet+magnet version is actually ECAS+magnet...

Can you please update / share the magnet+magnet option?

Cheers, Fred.

geoffrey-young, 2024-11-14:
which files are you referring to?  these are definitely the magnet+magnet
versions:

https://github.com/geoffrey-young/pika-filament-buffer/blob/main/stl/%5Ba%5D_buffer-top-magnet%2Bmagnet_xN.stl
https://github.com/geoffrey-young/pika-filament-buffer/blob/main/stl/10mm-magnets/%5Ba%5D_10mm-buffer-top-magnet%2Bmagnet_xN.stl

On Tue, Nov 12, 2024 at 5:09 PM Fred Maranhao ***@***.***>
wrote:

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

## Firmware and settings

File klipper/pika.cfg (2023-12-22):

# this is a helpful macro for easily testing toolhead unload/buffer load sequence
#
# !!! you must remove the bowden from the toolhead before running this macro.  you've been warned !!!
#
# the macro call will:
#
#  - select a tool
#  - prime the filament in the gate
#  - advance filament the length of the reverse bowden to simulate toolhead load
#  - advance filament to simulate extrusion
#  - retract filament the length of the reverse bowden to simulate toolhead unload
# 
#
# basic usage:
#
#  PIKA_TEST_BUFFER TOOL=[tool] BOWDEN=[ercf_calib_ref]
#
# available options:
#
#  TOOL:         the tool to test.  defaults to T0
#  BOWDEN:       length of the reverse bowden from the toolhead to the ercf.  should be roughly same as ercf_calib_ref.  defaults to 1200mm
#  UNLOAD_SPEED: unload speed, from toolhead into buffer.  defaults to 150mm/s
#  LOAD_SPEED:   load speed, from buffer into toolhead.  defaults to 150mm/s
#  EXTRUDE:      length of filament to "extrude."  defaults to 200mm
#  TIMES:        iterations of the load-extrude-unload cycle
#  LOOPS:        overrides BOWDEN.  number of loops around the wheel inside the pika, useful for buffer need vs capacity testing.  supports 1-8 loops.


[gcode_macro PIKA_TEST_BUFFER]
gcode:
  {% set loops = params.LOOPS | default(0) | int %}
  {% set bowden = params.BOWDEN | default(1200) | int %}
  {% set extrude =  params.EXTRUDE | default(200) | int %}
  {% set times = params.TIMES | default(1) | int %}
  {% set tool = params.TOOL | default(0, True) | int %}
  {% set uspeed = params.UNLOAD_SPEED | default(150) | int %}
  {% set lspeed = params.LOAD_SPEED | default(150) | int %}

  _PIKA_CHECK_HOMED

  {% set loops_to_bowden = ({
    1: 300,
    2: 600,
    3: 900,
    4: 1200,
    5: 1500,
    6: 1800,
    7: 2100, 
    8: 2300
  }) %}

  _PIKA_SELECT TOOL={tool}

  {% if loops %}
    {% set bowden = loops_to_bowden[loops] %}
  {% endif %}

  _PIKA_TEST_LOAD LENGTH=50

  _PIKA_CHECK_LOADED

  M118 {"starting test - iterations: %d, bowden: %d, extrude: %d" % (times, bowden, extrude) }

  {% for i in range(times) %}

    {% set e = extrude + (i*times) %}

    {% if i %}
      M118 settling...
      G4 P1000
    {% endif %}

    M118 simulating toolhead load...
    _PIKA_TEST_MOVE MOVE={bowden} SPEED={lspeed}
    M400

    M118 simulating extrude...
    _PIKA_TEST_MOVE MOVE={e} SPEED=10
    M400

    M118 buffering {bowden}mm at {uspeed}...
    _PIKA_TEST_MOVE MOVE=-{bowden} SPEED={uspeed}
    M400
  {% endfor %}

  _PIKA_SERVO_UP

  M118 test complete - gather filament


# and so begins compat...

[gcode_macro _PIKA_CHECK_LOADED]
gcode:
  {% if printer.mmu %}
    M118 XXX skipping load check for now...
  {% else %}
    {% if printer.ercf.loaded_status <= 0 %}
      { action_raise_error("filament not loaded - aborting") }
    {% endif %}
  {% endif %}

[gcode_macro _PIKA_CHECK_HOMED]
gcode:
  {% if printer.mmu %}
    {% if not printer.mmu.is_homed %}
      { action_raise_error("must home ercf first - aborting") }
    {% endif %}
  {% else %}
    {% if not printer.ercf.is_homed %}
      { action_raise_error("must home ercf first - aborting") }
    {% endif %}
  {% endif %}

[gcode_macro _PIKA_TEST_MOVE]
gcode:
  {% if printer.mmu %}
    MMU_TEST_MOVE MOTOR=gear {rawparams}
  {% else %}
    ERCF_TEST_MOVE_GEAR LENGTH={params.MOVE} {rawparams}
  {% endif %}

[gcode_macro _PIKA_SERVO_UP]
gcode:
  {% if printer.mmu %}
    MMU_SERVO POS=up
  {% else %}
    ERCF_SERVO_UP
  {% endif %}

[gcode_macro _PIKA_TEST_LOAD]
gcode:
  {% if printer.mmu %}
    MMU_TEST_LOAD {rawparams}
  {% else %}
    ERCF_TEST_LOAD {rawparams}
  {% endif %}

[gcode_macro _PIKA_SELECT]
gcode:
  {% if printer.mmu %}
    MMU_SELECT {rawparams}
  {% else %}
    ERCF_SELECT {rawparams}
  {% endif %}

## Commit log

2023-01-20 migration initial commit
    [array-back.stl, array-bottom-bracket-12.stl, array-bottom-bracket-6.stl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]
2023-02-12 remove for now. still available in git history...
    [buffer-screen-b-long.stl]
2023-02-26 add filament direction labeling add edge to tops to help with loose and end slots (thanks again @ningj!)
    [buffer-top-ecas+ecas.stl, buffer-top-ecas+magnet.stl, buffer-top-magnet+magnet.stl]
2023-03-11 fix missing bevel. thanks, Razamanaz!
    [array-back.stl]
2023-03-21 make bearing insert longer so it's less likely to break
    [buffer-bearing-insert.stl]
2023-03-27 stronger posts
    [buffer-screen-b.stl]
2023-03-31 add filament pointers
    [buffer-wheel.stl]
2023-03-31 replace ingress/egress words with more universal images
    [buffer-top-ecas+ecas.stl, buffer-top-ecas+magnet.stl, buffer-top-magnet+magnet.stl]
2023-04-04 minor tweaks
    [buffer-top-ecas+ecas.stl, buffer-top-ecas+magnet.stl, buffer-top-magnet+magnet.stl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]
2023-04-05 add direction arrow for assembly guidance tidy bevels
    [buffer-bottom.stl]
2023-04-05 add direction arrow for assembly guidance
    [array-latch-12a.stl, array-latch-12b.stl, array-latch-6a.stl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]
2023-04-06 add what qualifies as my effort for an assembly manual...
2023-04-07 add assembly manual links
2023-04-07 add assembly manual image placeholder
2023-04-10 add missing bevel. tidy.
    [buffer-top-ecas+magnet.stl]
2023-04-10 rename buffer-bowden-magnet-end.stl to ecas-to-magnet.stl and update
    [buffer-bowden-magnet-end.stl, ecas-to-magnet-end.stl]
2023-05-23 migrate screen from hex nut to heatset (thanks ZChem) PR 3
    [buffer-screen-a.stl]
2023-05-23 fix manifold errors. oops :/
    [buffer-screen-a.stl]
2023-05-29 update amazon magnet info
2023-05-29 move to voron-style stl naming
    [[a]_buffer-bearing-insert_xN.stl, [a]_buffer-handle_xN.stl, [a]_buffer-screen-a_xN.stl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]
2023-05-30 update counts for heatset
2023-06-09 add support for 10x3mm magnets
    [[a]_10mm-buffer-top-ecas+magnet_xN.stl, [a]_10mm-buffer-top-magnet+magnet_xN.stl, [a]_10mm-ecas-to-magnet-end_xN.stl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]
2023-06-09 better magnet docs
    [magnet-test-blocks.stl]
2023-06-19 remove ecas+ecas option. y'all can thank me later...
    [[a]_buffer-top-ecas+ecas_xN.stl]
2023-06-19 making the ercf journey better, one magnet at a time...
2023-07-03 fix magnet bom counts
2023-07-27 tidy models
    [[a]_10mm-buffer-top-ecas+magnet_xN.stl, [a]_10mm-buffer-top-magnet+magnet_xN.stl, [a]_buffer-top-ecas+magnet_xN.stl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]
2023-08-04 extend m3x8 holes to m3x10
    [[a]_10mm-buffer-top-ecas+magnet_xN.stl, [a]_10mm-buffer-top-magnet+magnet_xN.stl, [a]_buffer-top-ecas+magnet_xN.stl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]
2023-08-04 add testing macro
    [pika.cfg]
2023-08-04 add cad readme
2023-08-24 add some comments on the wheel...
2023-09-15 define m3 heatset dimensions update happy hare link
2023-09-25 start of happy hare v2 support...
    [pika.cfg]
2023-11-04 reduced heatset holes to 4.6mm diameter
    [[a]_buffer-screen-a_xN.stl, buffer-bottom_xN.stl]
2023-11-04 add 3 cart latches and bottom (https://github.com/geoffrey-young/pika-filament-buffer/pull/9)
    [array-bottom-bracket-3.stl, array-latch-3a.stl, array-latch-3b.stl]
2024-03-29 add 8 cart bracket and latches
    [array-bottom-bracket-8.stl, array-latch-8a.stl, array-latch-8b.stl]
